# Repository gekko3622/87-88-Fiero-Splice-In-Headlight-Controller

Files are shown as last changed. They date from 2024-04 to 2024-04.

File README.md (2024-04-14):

# 1987-1988 Pontiac Fiero Headlight Motor Controller
**PCB Designed by Ryan Blanchard 4.2024**\
**Based On A Project by WalkerTexan** (See credits section for details and link)\
**FOR NON-COMMERCIAL USE ONLY.**

**NEW! V2.2 has been added which supports internal ATC fuses for the motor power inputs.**\
**V2.1 has been retained in the repository for those who want to use external inline fuses or don't feel the need to.**

\
**Note:** This is my personal PCB, based on version 2.0. The files contained in this project are version 2.2 and 2.1.\
V2.2 adds provisions for standard ATC fuses on the main 12V lines to the motors. Other minor trace routing optimizations were added as well.\
V2.1 is electrically identical to V2.0. The only changes made were to reposition and enlarge some of the silkscreen label text for legibility.

## Intro
This project is a PCB implementation of WalkerTexan's "Fiero Headlight Controller".\
I started this 	project after getting frustrated with the cost and questionable reliability of used modules.\
While there are also new production versions of the original module available now, I found the cost to be way too high.

## Purpose and Origin
I started this project to replace the second failed module in my 87 Pontiac Fiero.\
It started as a basic DIY project and grew into a proper PCB design after my prototype proved to be reliable.

Pictured here is my original DIY prototype. The PCB version is night-and-day BEAUTIFUL compared to this thing.

image0(1)

## Repository Contents

**Items 2 and 3 are now contained within version numbered folders.**

**1. Arduino Nano Program**
- WalkerTexan's code for the Arduino Nano.\
This MUST be programmed onto the Arduino for the module to function. The same file is used for V2.2 and V2.1.

**2. Gerber Files (For Production)**
- These are the files that must be provided to a fabricator to produce a PCB.\
  **VERY IMPORTANT:** This PCB MUST be produced with 2 Oz copper weight in order to meet power handling requirements.\
  The provided gerber files will produce an electrically identical copy of the PCB installed in my own car.

  The provided Zip file can be directly submitted to a fabricator and contains all of the other individual files in this folder.

**3. KiCad Project Files**
- These are my original KiCad 8.0 project files.\
  You will need these if you intend to make any alterations to the PCB's design.

## Installation Location
This module is designed to be installed under the hood, in the area around the brake master cylinder.\
This allows for easier access and makes it possible to install without damaging the original connectors.\
NOTE: Installing this module will require you to cut and slice a new connector onto the original front wiring harness.

## Wiring Guide
You will need to provide two sets of waterproof automotive connectos for this project.\
For the sake of this writeup, I'll assume you have 5-pin and 4-pin connector sets.\
Connector/pin numbers are based on the labels printed on my version of the PCB (See image below).\
Wire colors give are for the wires contained in the factory wiring harness, which runs inside the frunk, driver side.\
If you make changes, you will need to determine your own wiring scheme.

V2 2 board

**SAFETY WARNING: Please splice into the wiring harness after any fusible links. They are there for a reason.**

### To Wiring Harness
	
C1-1  -  Connect to red wire on harness. (there are two, both will be used)\
C1-2  -  Connect to ground. I recommend running a new ground wire. The harness contains MANY black ground wires.\
C1-3  -  Connect to white wire on harness.\
C1-4  -  Connect to other red wire on harness.\
C1-5  -  Connect to yellow wire on wiring harness.

### To Headlight Motors
		
C2-1  -  Light Green/Black\
C2-2  -  Gray/Black\
C2-3  -  Dark Green\
C2-4  -  Gray

**You may want to run new wires and connectors to the headlight motors to preserve original wiring.**

I used a generic equivalent of AC Delco PT724.\
The connector has notches cut into the plastic pin barrels. These do not match the notches on the headlight motor connector.\
I solved this problem by heating a knife with a lighter and cutting my own matching notches into the new connectors.

If you go this route, cut the new notches as indicated in red on this image:\


## Component List
See BOM.xlsx for a full list of required components.

## Enclosure
The PCB is intended to be installed within a water-resistant project box.\
The specific box I used is this: https://www.amazon.com/dp/B075WZFWFV?th=1  
Any enclosure with space for a 170mm x 110mm PCB could be used, though mounting hole pattern should be considered.\
Keep in mind there needs to be some space for the wiring too.



**PCB Mounting Holes (center to center):** 160 mm x 90 mm

## Modifications to Original Source
1. Recreated the schematic diagram in KiCad.
2. Designed a PCB based on the schematic.
3. Substituted the 5V relays for an alternate part with higher current rating.
4. Added detachable headers and connectors for connecting to the car's wiring.

## Credits
The electrical schematic and Arduino code this project is based on were created by WalkerTexan.\
See his original project here: https://www.hackster.io/walkertexan/fiero-headlight-controller-8eaa4c

KiCad Schematic and PCB Layout/Design by Ryan Blanchard.

## License
This project is published under the Creative Commons Attribution-NonCommercial-ShareAlike 4.0 International license.\
Use of this project for commercial purposes is prohibited.

For full details, see the license file.

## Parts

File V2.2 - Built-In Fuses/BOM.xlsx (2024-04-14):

Required
Component | Quantity | Position | Link | Note
Arduino Nano | 1 | A1 | https://store-usa.arduino.cc/products/arduino-nano | Cheaper third-party alternatives are available, if you trust them. I personally used this clone board: https://www.amazon.com/dp/B09KGVDXZY
HiLetgo 2pcs ACS712 30A Current Sensor Module | 2 | U2, U3 | https://www.amazon.com/HiLetgo-ACS712-Current-Sensor-Module/dp/B07SPRL8DL | Sold as a 2-pack. You will need to desolder the right angle pins and terminals. The modules will connected to the board by soldered pin headers.
JQC-3FF-S-Z 12V Relay | 1 | K5 | https://www.amazon.com/uxcell-JQC-3FF-S-Z-Electromagnetic-Power-Relay/dp/B07JGSL4F3
J107F1CS205VDC.45 Relay | 4 | K1, K2, K3, K4 | https://www.digikey.com/en/products/detail/cit-relay-and-switch/J107F1CS205VDC-45/14000915/ | Original project called for SRD-05VDC-SL-C relays. I specced these alternatives for their higher current rating for worst case scenarios.
1N4001 Rectifier Diode | 5 | CR1, CR2,CR3,CR4, CR5 | https://www.amazon.com/BOJACK-Rectifier-IN4001-Electronic-Silicon/dp/B07Q3HBM63
2N2222A Transistor | 8 | Q1, Q2, Q3, Q4, Q5, Q6, Q7, Q8 | https://www.amazon.com/CHANZON-BJT-Transistors-2N2222A-TO-92-100/dp/B083TNXLHD
5mm Red LED | 4 | D1, D2, D3, D4 | https://www.amazon.com/dp/B077X95F7C | You will not use the included resistors.
1K 0.25w Resistor | 7 | R2, R4, R5, R6, R7, R8, R9 | https://www.amazon.com/dp/B0B4G8HQD1
10K 0.25w Resistor | 3 | R1, R3, R10 | https://www.amazon.com/dp/B0B4JFPHTW
200 ohm 0.25w Resistor | 4 | R11, R12, R13, R14 | https://www.amazon.com/dp/B07HDGH1R1
L7805CV Voltage Regulator | 1 | U1 | https://www.amazon.com/Chanzon-Three-Terminal-Positive-Regulator-Transistor/dp/B083TBMJJS
10UF 25V Capacitor | 2 | C1, C2 | https://www.amazon.com/Projects-Radial-Electrolytic-Capacitor-10uF/dp/B07YBCF9NG
5 pin waterproof connector | 1 | N/A | https://www.amazon.com/dp/B085HNSVY4
4-pin waterproof connector | 1 | N/A | https://www.amazon.com/dp/B085HD43H1 | You can cost save on this by using a 5-pin for both sides, but be SURE to label everything extensively so you don't plug the module in backwards. I'd just spend the extra money to make it foolproof.
2.54mm Breakaway Header/Pins | 1 Package | A1, U2, U3 | https://www.amazon.com/gp/product/B08DVGCTKT | Used to socket the Arduino and also to mount the current sensors. For current sensors, you will use 4 segments of 3-pin connector. For two of them, remove the middle pin. You'll see where they go.
ATC Fuse Holder | 2 | F1, F2 | https://www.amazon.com/Uxcell-a14052300ux0215-Truck-Blade-Holder/dp/B00OK9H3EI/ | Also purchase ATC fuses of your choice. 15A may be too low given the normal momentary current spike at full open/close. 20A may be better.
Optional These items are optional, but will give you a much more polished installation. Specialized crimper required.
Component | Quantity | Position | Link | Note
Molex 1724480006 6-pin Header | 1 | J1 | https://www.digikey.com/en/products/detail/molex/1724480006/5116920 | Nicer alternative to soldering the waterproof connectors directly to the PCB.
Molex 1724480004 4-pin Header | 1 | J2 | https://www.digikey.com/en/products/detail/molex/1724480004/5116919 | Nicer alternative to soldering the waterproof connectors directly to the PCB.
Molex 0469920610 Connector | 1 | N/A | https://www.digikey.com/en/products/detail/molex/0469920610/5116009 | Matching connector for 1724480006
Molex 0469920410 Connector | 1 | N/A | https://www.digikey.com/en/products/detail/molex/0469920410/5116008 | Matching connector for 1724480004
Molex 0039000060 Crimp-On Pins | 10 | N/A | https://www.digikey.com/en/products/detail/molex/0039000060/1118558 | Crimp-on pins required for the above connectors. Requiures a crimper such as https://www.amazon.com/dp/B08CZDRV4N A normal butt splice crimper will not work for these!

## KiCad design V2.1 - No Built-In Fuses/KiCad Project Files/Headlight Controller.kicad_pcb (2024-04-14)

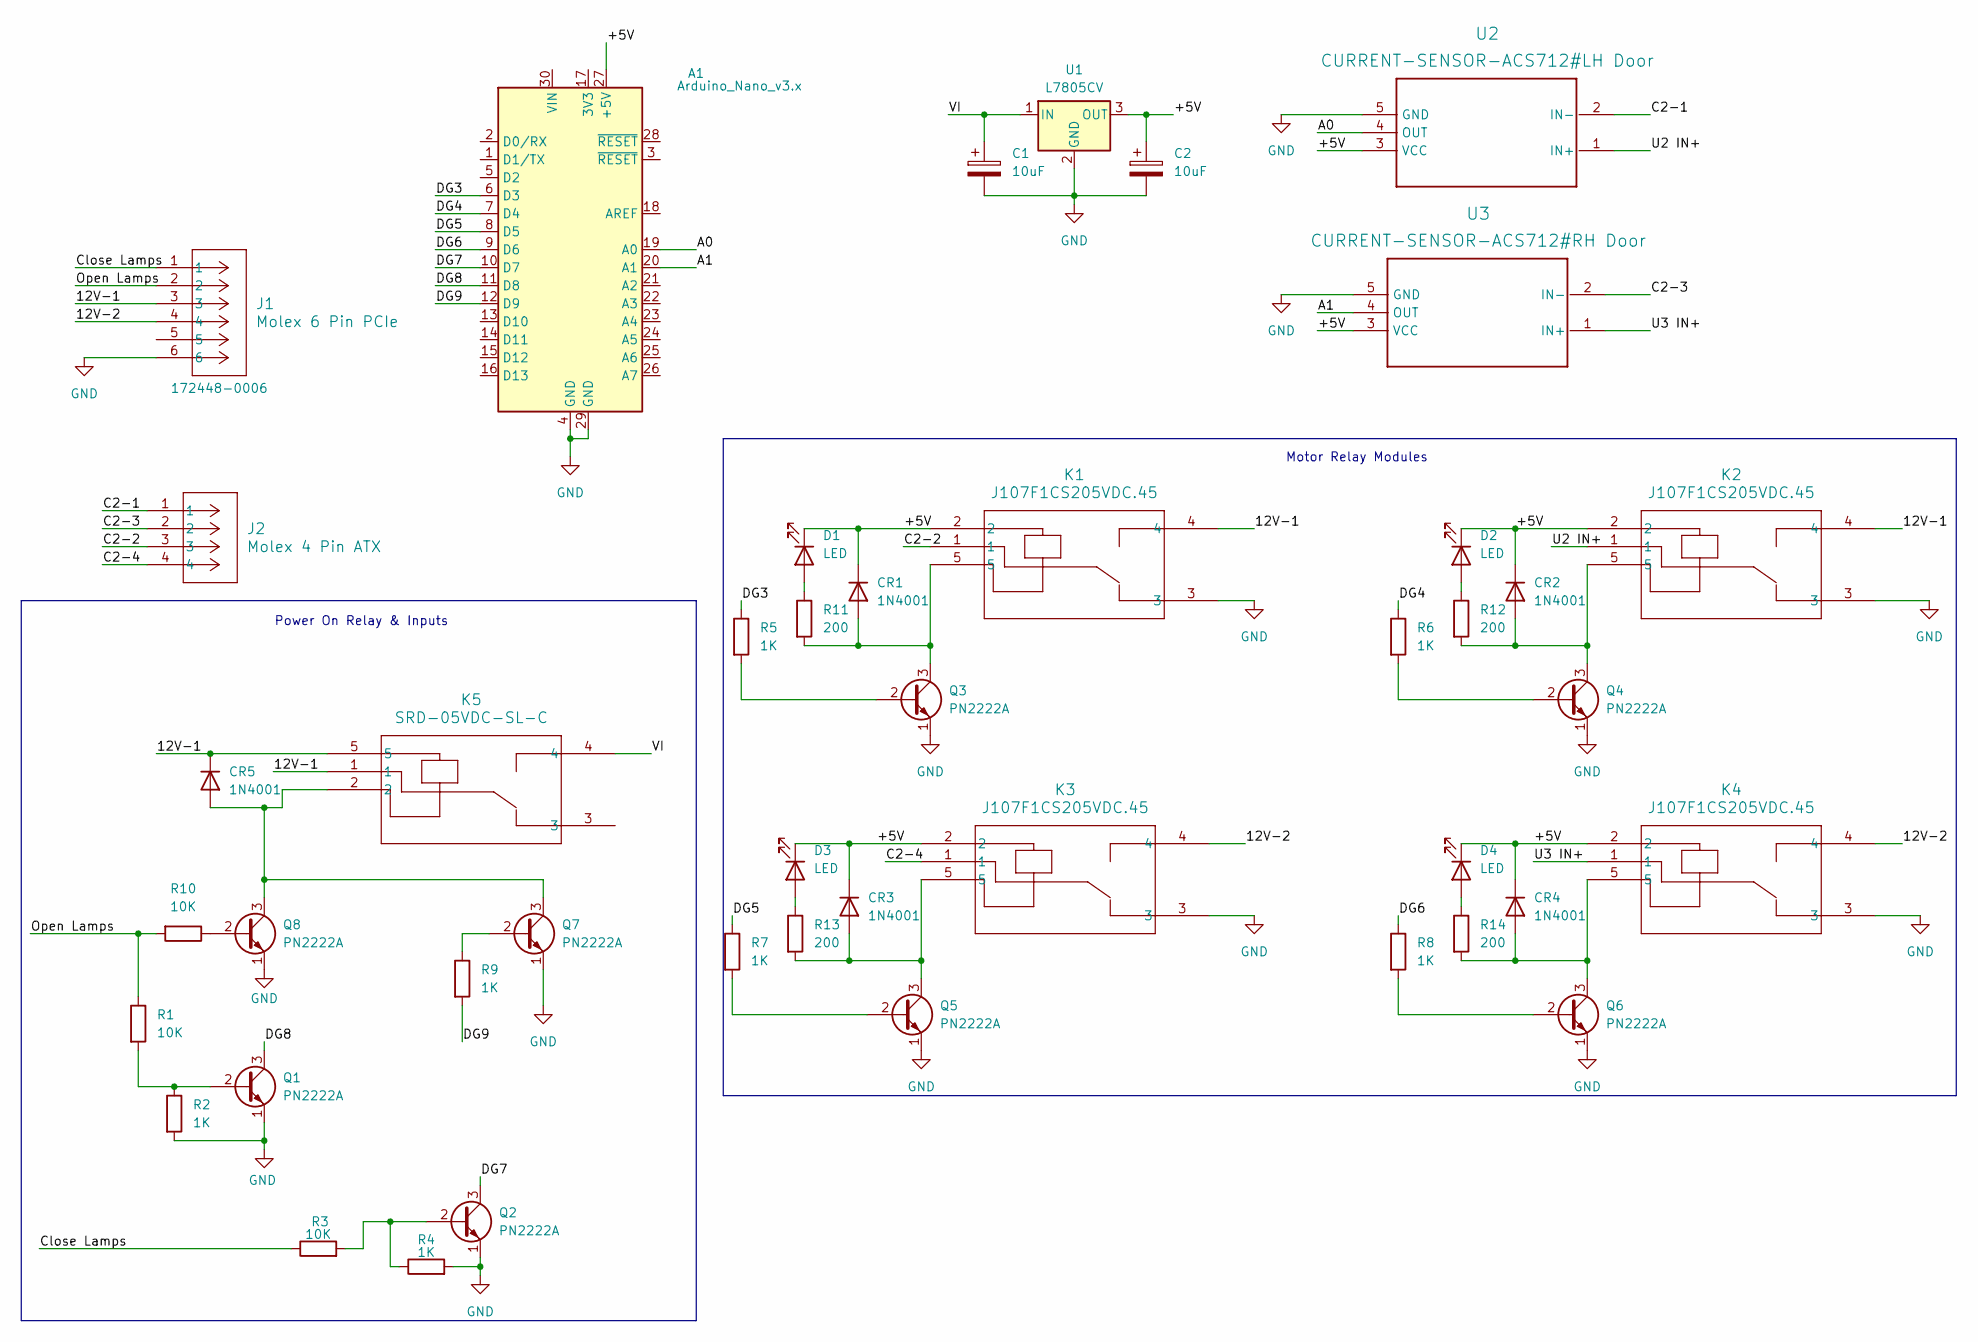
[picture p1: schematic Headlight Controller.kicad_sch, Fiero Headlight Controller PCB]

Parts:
A1: Arduino_Nano_v3.x; Arduino_Nano
C1, C2: 10uF; CAP-TH_BD5.0-P2.00-D0.8-FD
CR1, CR2, CR3, CR4, CR5: 1N4001; DIODE-1N4001
D1, D2, D3, D4: LED; LED-5MM-5MM
J1: Molex 6 Pin PCIe; 6 Pin PCIe
J2: Molex 4 Pin ATX; 4 Pin ATX
K1, K2, K3, K4: J107F1CS205VDC.45; JQC-3FF-S-Z
K5: SRD-05VDC-SL-C; JQC-3FF-S-Z
Q1, Q2, Q3, Q4, Q5, Q6, Q7, Q8: PN2222A; 2N2222A
R1, R3, R10: 10K; Resistors
R2, R4, R5, R6, R7, R8, R9: 1K; Resistors
R11, R12, R13, R14: 200; Resistors
U1: L7805CV; L7805
U2: CURRENT-SENSOR-ACS712#LH Door; ACS712_A
U3: CURRENT-SENSOR-ACS712#RH Door; ACS712_A

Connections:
/12V-1: CR5.C (K), J1.3, K1.4, K2.4, K5.1, K5.5
/12V-2: J1.4, K3.4, K4.4
/+5V: A1.27 (+5V), C2.1, CR1.C (K), CR2.C (K), CR3.C (K), CR4.C (K), D1.1 (K), D2.1 (K), D3.1 (K), D4.1 (K), K1.2, K2.2, K3.2, K4.2, U1.3 (OUT), U2.3 (VCC), U3.3 (VCC)
/A0: A1.19 (A0), U2.4 (OUT)
/A1: A1.20 (A1), U3.4 (OUT)
/C2-1: J2.1, U2.2 (IN-)
/C2-2: J2.3, K1.1
/C2-3: J2.2, U3.2 (IN-)
/C2-4: J2.4, K3.1
/Close Lamps: J1.1, R3.1
/DG3: A1.6 (D3), R5.1
/DG4: A1.7 (D4), R6.1
/DG5: A1.8 (D5), R7.1
/DG6: A1.9 (D6), R8.1
/DG7: A1.10 (D7), Q2.3 (C)
/DG8: A1.11 (D8), Q1.3 (C)
/DG9: A1.12 (D9), R9.2
/Open Lamps: J1.2, R1.1, R10.2
/U2 IN+: K2.1, U2.1 (IN+)
/U3 IN+: K4.1, U3.1 (IN+)
/VI: C1.1, K5.4, U1.1 (IN)
GND: A1.4 (GND), A1.29 (GND), C1.2, C2.2, J1.6, K1.3, K2.3, K3.3, K4.3, Q1.1 (E), Q2.1 (E), Q3.1 (E), Q4.1 (E), Q5.1 (E), Q6.1 (E), Q7.1 (E), Q8.1 (E), R2.2, R4.2, U1.2 (GND), U2.5 (GND), U3.5 (GND)
unnamed: D1.2 (A), R11.1
unnamed: D2.2 (A), R12.1
unnamed: D3.2 (A), R13.1
unnamed: D4.2 (A), R14.1
unnamed: Q1.2 (B), R1.2, R2.1
unnamed: Q2.2 (B), R3.2, R4.1
unnamed: Q3.2 (B), R5.2
unnamed: CR1.A, K1.5, Q3.3 (C), R11.2
unnamed: Q4.2 (B), R6.2
unnamed: CR2.A, K2.5, Q4.3 (C), R12.2
unnamed: Q5.2 (B), R7.2
unnamed: CR3.A, K3.5, Q5.3 (C), R13.2
unnamed: Q6.2 (B), R8.2
unnamed: CR4.A, K4.5, Q6.3 (C), R14.2
unnamed: Q7.2 (B), R9.1
unnamed: CR5.A, K5.2, Q7.3 (C), Q8.3 (C)
unnamed: Q8.2 (B), R10.1

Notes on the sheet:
Motor Relay Modules
Power On Relay & Inputs

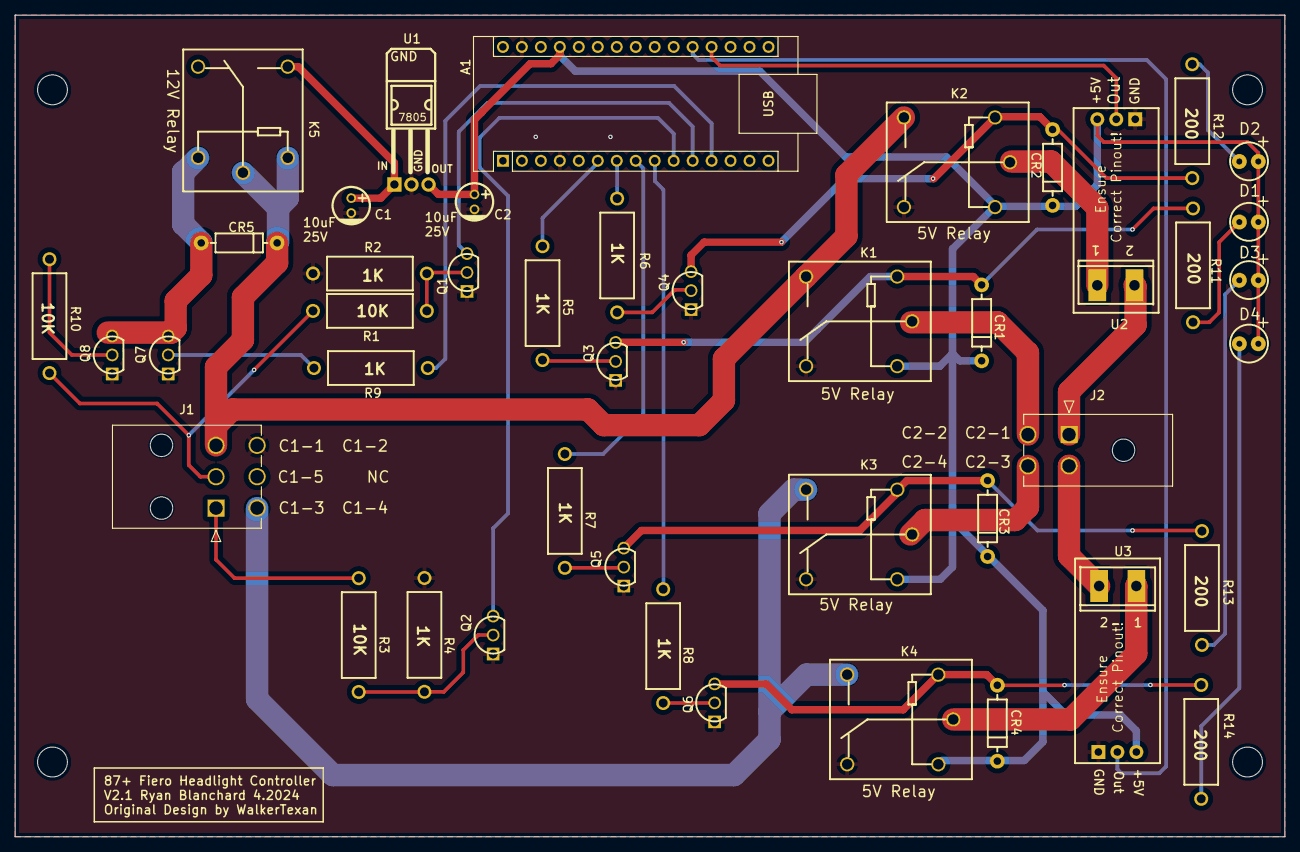
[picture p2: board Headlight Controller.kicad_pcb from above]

Board: 2 copper layers, 170.0 x 110.0 mm, 44 parts (0 on the bottom side), 39 nets.

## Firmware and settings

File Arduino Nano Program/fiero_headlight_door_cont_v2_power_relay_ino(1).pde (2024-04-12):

//POWER RELAY version
//This program along with the circuitry replaces the Fiero Headlight Door Module with
//a modern equivalent.  The module in my car is dead so this has become a necessity.
//NOTE THAT THIS is a fix for 87 and 88 modules and NOT the prior design although
//it may be reasonably simple to implement for those if necessary.

//The Fiero Light switch produces two signals: one is at 12V when the lights are off
//while the other is at 12V when the lights are on.  Both are floating and essentially
//at ground potential when the parking lights are on.

//The original circuit performed a crude H bridge using a 4PDT relay which is an
//expensive component and hard to find in a format that fits the original module.  This
//approach uses four SPDT relays in an Arduino-compatible module to form the H bridge.
//The relay module is designed as active-low on the input signals.

//The original circuit used programmable logic to sense the current draw of each motor.
//If the motor stalled at either the ends or during travel then a high current would
//occur and the logic would remove power from the offending motor.  The relay in the
//circuit was limited to 5A so it is assumed that the maximum allowable continuous
//current was less than this.  Bad assumption.  GM did a poor design because the current
//is closer to 12A inrush as measured with an ammeter, although for short duration.  This explains
//the failed relays over the years and possibly causes the failures of the FETs.
//This approach uses two hall-effect Arduino-compatible current sensors to detect
//this condition so that power is removed quickly.

//The original circuit also provided a timer of approximately 2.5 seconds for the
//motors to reach either open or closed position.  This approach will do this as well.

//Program written by Michael Walker Copyright 03/2021.  Program is free for use without
//any warranty either expressed or implied.

int LH_zero_current, RH_zero_current; //values read to "calibrate" the current sensors
int Current_limit;
int count, Loop_count;
int current_value;
void Open_doors();//routine opens the doors and checks for damaging current
void Close_doors();//routine closes the doors and checks for damaging current


void setup()
{
  // pinitialization will occur when power is applied to the circuit through the 12V relay, i.e. when the
  //headlight switch is ON.  The lighting circuits have live power through that relay only.
  //TURN ON THE RELAY DRIVER IMMEDIATELY TO KEEP POWER ON THE CIRCUIT!  This driver allows the circuit
  //to remain ON when the switch is turned OFF long enough to retract the lights.
  //The circuit remains LIVE as long as the lights are ON once this is initiated; you must turn OFF the 
  //headlights in order to remove power from the circuit.

    pinMode(9, OUTPUT);//driver control for the 12V relay to power the module
    digitalWrite(9, HIGH);//keep the power ON until the doors are closed.
    
  //Keep this is mind when servicing any of the headlight components because they
  //can actuate at any time if the headlight switch is ON!
//  Serial.begin(9600);//debug and will probably be removed later.
//  Serial.println("Fiero Headlight Door Module V2 is Alive and Well!");

  //Current sensor ACS712/30A centers at 2.5V at zero current when operating with a 5V supply.  The
  //output is proportional to the current with 66mV equivalent to 1A.  The Arduino Nano A/D is 10-bit
  //so each count is 5/1024 or 4.88mV (14 counts per amp).  At zero current the value should be approximately 512.  A 5A
  //value should be approximately 5 * 66mV or 330mv.  That corresponds to a count of 330mV/4.88mV
  //which is approximately 68 counts above the zero current value. A value of 27 would be approximately
  //2A and 41 would be 3A.  Experimentation shows that the inrush current of the motor is approximately 
  //8A and sometimes triggers an overcurrent up to about 11A.  This means that the overcurrent level 
  //needs to be at least 12A and possibly more to account for ambient temperature.  A value of 14.8A
  //seems to give perfect results without overcurrent occurring and is low enough to prevent burnout of
  //the motor or the fuse links while accounting for higher current during cold conditions.
  //Increasing the delay time at initial startup to account for inrush might be a better approach since the
  //current limit could be lowered to a value closer to 8A and may be implemented in the future if it seems
  //prudent.
  Current_limit = 200; //approximately 14.8A above the "zero current" value to account for inrush current
  Loop_count = 150;  //number of loops with 10ms delay to equal 2.5 seconds. Accounting for A/D reads
                    //and logic every 10ms makes this number less than expected 250. Matches original system.
  //define the DIO pins
  pinMode(3, OUTPUT);//LH OPEN drive
  pinMode(4, OUTPUT);//LH CLOSE drive
  pinMode(5, OUTPUT);//RH OPEN drive
  pinMode(6, OUTPUT);//RH CLOSE drive
  pinMode(7, INPUT_PULLUP);//C1-C white wire CLOSE headlight switch signal
  pinMode(8, INPUT_PULLUP);//C1-A yellow wire OPEN headlight switch signal

  digitalWrite(3, LOW);   // turn off LH OPEN drive
  digitalWrite(4, LOW);   // turn off LH CLOSE drive
  digitalWrite(5, LOW);   // turn off RH OPEN drive
  digitalWrite(6, LOW);   // turn off RH CLOSE drive
 
  //Power has been applied so headlights were commanded. Open the doors.
  Open_doors();
  
}//end of setup

void loop()
{


  //The loop will check the condition of the two Headlight switch signals every
  //100ms.  The signals are active LOW to the circuit.

  //If DG7 is low and DG8 is high then the light switch is off so the doors are ordered CLOSED.
  if (digitalRead(7) == LOW && digitalRead(8) == HIGH)
  {
//       Serial.println("Light Switch is OFF ");//debug
    Close_doors();
  }

  delay(100);//wait 100ms before checking again
}// end of loop

void Open_doors()
{
  //This routine commands the LH and RH doors to OPEN and allows 2.5 seconds for
  //that to happen.  The current is monitored every 10ms and if it exceeds the
  //base zero current value plus/minus the high limit value then power is immediately
  //removed from the OPEN relay for the bad door.
  //The relays are turned off after the 2.5 seconds has
  //transpired unless turned off sooner due to overcurrent.

  //If the overcurrent only happens on one door then that door will likely be left
  //in a partially open state.  This allows you to detect which door was the problem
  //in case it isn't obvious for other reasons, like bad noises.  If nothing else
  //it allows you to crank the light to the proper position while the other remains
  //usable.

  Serial.println("Open Doors now");
    
  //no current should be present through the motors at this point so find the quiescent
  //value from the sensors
  LH_zero_current = analogRead(0); //this should be approximately 512 counts
  RH_zero_current = analogRead(1); //this should be approximately 512 counts
  Serial.print("Zero Current LH=");
  Serial.println(LH_zero_current);
  Serial.print("Zero Current RH=");
  Serial.println(RH_zero_current);
  count = 0;
  //Make sure CLOSE signals are OFF
  digitalWrite(4, LOW); //close is off for LH
  digitalWrite(6, LOW); //close is off for RH
  //now turn ON OPEN signals
  digitalWrite(3, HIGH);//LH is on
  digitalWrite(5, HIGH);//RH is on

  while (count < Loop_count) //wait for doors to complete operation or overcurrent happens
  {
    current_value = analogRead(0);//LH current reading
    //overcurrent? shut LH down
    if (current_value > (LH_zero_current + Current_limit)) 
    {
      Serial.print("Overcurrent LH=");
      Serial.println(current_value);  
      digitalWrite(3, LOW);
    }
    if (current_value < (LH_zero_current - Current_limit))
    {
      Serial.print("Overcurrent LH=");
      Serial.println(current_value); 
      digitalWrite(3, LOW);
    }
    current_value = analogRead(1);//RH current reading
   
    //overcurrent? shut RH down
    if (current_value > (RH_zero_current + Current_limit))
    {
      Serial.print("Overcurrent RH=");
      Serial.println(current_value);
      digitalWrite(5, LOW);
    }
    if (current_value < (RH_zero_current - Current_limit))
    {
      Serial.print("Overcurrent RH=");
      Serial.println(current_value);
      digitalWrite(5, LOW);
    }
    if (count == 0) 
    {
      delay(50); //allow 50ms for inrush
    }
    else 
    {
      delay(10); //wait 10ms and check again
    }
    
    count++;
  } //end of while(count < 250)

  //done, turn off OPEN relays
  digitalWrite(3, LOW);//LH is off
  digitalWrite(5, LOW);//RH is off
}//end of Open_doors

void Close_doors()
{
  //This routine commands the LH and RH doors to CLOSE and allows 2.5 seconds for
  //that to happen.  The current is monitored every 10ms and if it exceeds the
  //base zero current value minus the high limit value then power is immediately
  //removed from the CLOSE relay for the bad door. 
  //The relays are turned off after the 2.5 seconds has
  //transpired unless turned off sooner due to overcurrent.

  //If the overcurrent only happens on one door then that door will likely be left
  //in a partially open state.  This allows you to detect which door was the problem
  //in case it isn't obvious for other reasons, like bad noises.  If nothing else
  //it allows you to crank the light to the proper position while the other remains
  //usable.

  Serial.println("Close Doors now");

  //no current should be present through the motors at this point so find the quiescent
  //value from the sensors
  LH_zero_current = analogRead(0); //this should be approximately 512 counts
  RH_zero_current = analogRead(1); //this should be approximately 512 counts
  Serial.print("Zero Current LH=");
  Serial.println(LH_zero_current);
  Serial.print("Zero Current RH=");
  Serial.println(RH_zero_current); 
  
  count = 0;
  //Make sure OPEN signals are OFF
  digitalWrite(3, LOW); //open is off for LH
  digitalWrite(5, LOW); //open is off for RH
  //now turn ON CLOSE signals
  digitalWrite(4, HIGH);//LH is on
  digitalWrite(6, HIGH);//RH is on

  while (count < Loop_count) //wait for doors to complete operation or overcurrent happens
  {
    current_value = analogRead(0);//LH current reading
    
    //overcurrent? shut LH down
    if (current_value > (LH_zero_current + Current_limit))
    {
      Serial.print("Overcurrent LH=");
      Serial.println(current_value);
      digitalWrite(4, LOW);
    }
    if (current_value < (LH_zero_current - Current_limit))
    {
      Serial.print("Overcurrent LH=");
      Serial.println(current_value);
      digitalWrite(4, LOW);
    }
    current_value = analogRead(1);//RH current reading
    
    //overcurrent? shut RH down
    if (current_value > (RH_zero_current + Current_limit))
    {
      Serial.print("Overcurrent RH=");
      Serial.println(current_value);
      digitalWrite(6, LOW);
    }
    if (current_value < (RH_zero_current - Current_limit))
    {
      Serial.print("Overcurrent RH=");
      Serial.println(current_value);
      digitalWrite(6, LOW);
    }
  if (count == 0) 
    {
      delay(50); //allow 50ms for inrush
    }
    else 
    {
      delay(10); //wait 10ms and check again
    }
       count++;
  } //end of while(count < 250)

  //done, turn off CLOSE relays
  digitalWrite(4, LOW);//LH is off
  digitalWrite(6, LOW);//RH is off
  digitalWrite(9, LOW);//turn off power to stop drain on battery. Module will stop operating
  delay(500); //wait for power to bleed off. Should be gone long before this times out.
  
}//end of Close_doors

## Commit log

2024-04-12 Add files via upload
    First file upload. Contains only the base project files and gerber files.
    [Headlight Controller-B_Cu.gbr, Headlight Controller-B_Mask.gbr, Headlight Controller-B_Paste.gbr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]
2024-04-12 Update README.md
    Added enclosure information, minor tweaks.
2024-04-12 Update README.md
    Updated BOM information. Removed reference to wiki, as I won't be using it.
2024-04-12 Added BOM.xlsx
    Added the BOM.
    [BOM.xlsx]
2024-04-12 Added Arduino Nano Program
2024-04-13 Updated BOM
    [BOM.xlsx]
2024-04-14 Updated BOM: pin headers/Alternative Arduino
    [BOM.xlsx]
2024-04-14 Added V2.2 - Internal Fuses
    Version 2.2 has mounting holes to solder ATC fuses directly or in a holder.
    V2.1 retained for those who would prefer to use inline external fuses.
    [BOM.xlsx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]
2024-04-15 Removed old/unnecessary files
    [Headlight Controller-B_Cu.gbr, Headlight Controller-B_Mask.gbr, Headlight Controller-B_Paste.gbr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]
